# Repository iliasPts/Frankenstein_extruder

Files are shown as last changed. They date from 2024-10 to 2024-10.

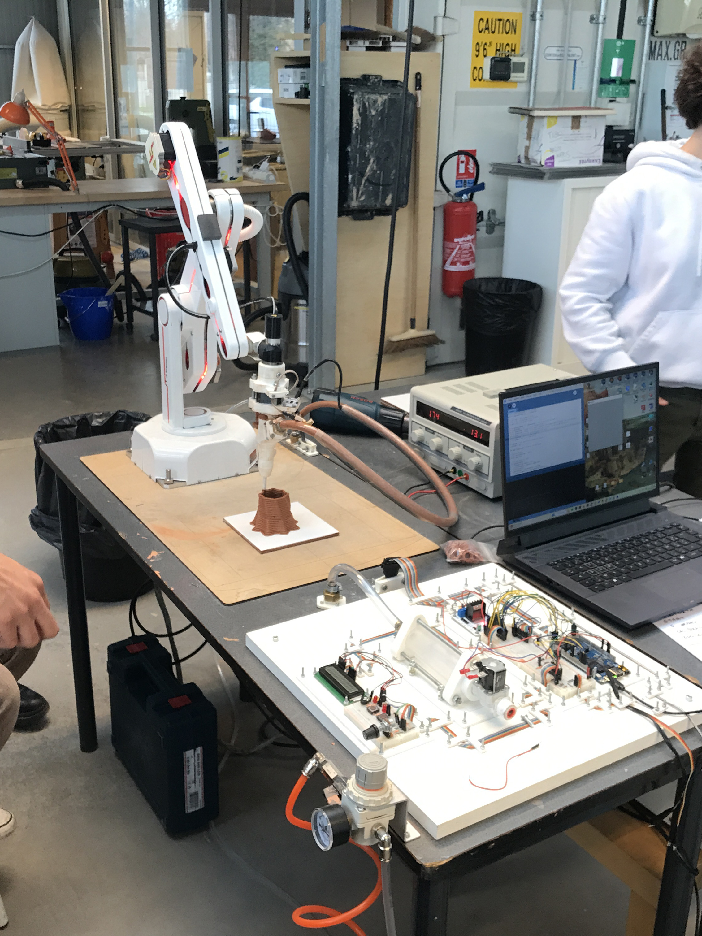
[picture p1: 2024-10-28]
Photos/Photo 2.jpg

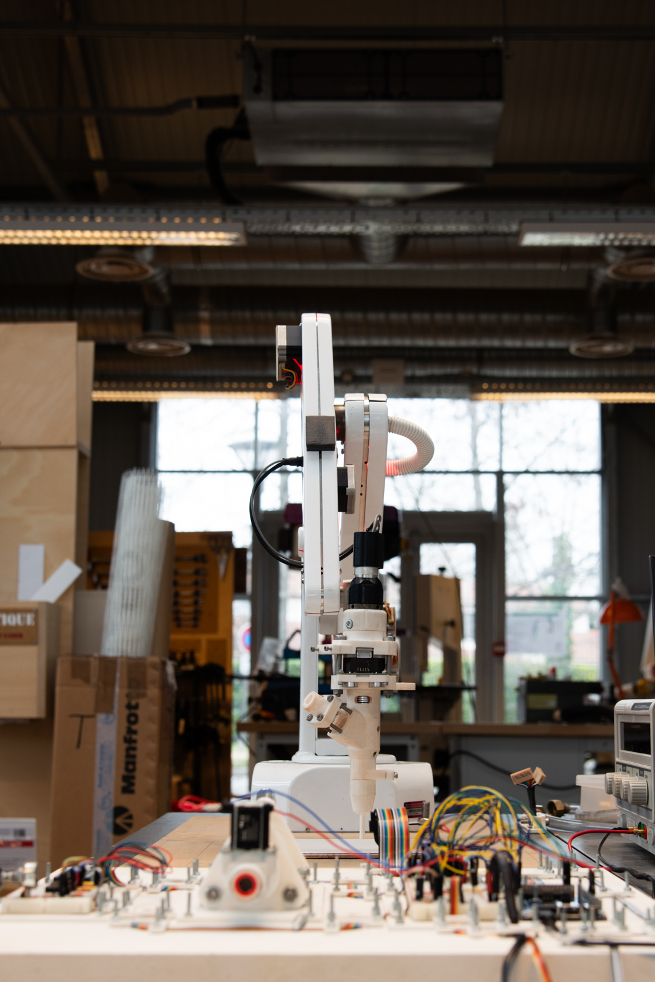
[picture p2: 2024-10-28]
Photos/Photo 5.jpg

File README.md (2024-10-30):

# Frankenstein_extruder
#### Frankenstein is an extruder built for modularity and versatility. Designed with affordability in mind, it’s initially tailored for articulated robots but adaptable to various numerically controled machines, including 3D printers.

Its distinctive feature is the complete accessibility of its components, fully exposed to the view like a body laid open for dissection. This openness allows users to configure countless setups by rearranging electronic, pneumatic, and hose connections.  This modularity is also made possible by the implementation of new programs (in arduino format) enabling new functions. In this way, the system can be expanded by adding new components (e.g. extrusion control sensors) that take advantage of the many electronic lines left available for this very purpose.

Beyond flexibility, Frankenstein is designed for interactive operation (with operators or data exterior to the system), incorporating multiple input and output interfaces (buttons, knobs, LCD displays, sensors, etc.), all programmable to meet specific user needs. This makes it particularly valuable in educational and research contexts.

#### Frankenstein is therefore not an extruder driven by precision or reliability, but by exploration, creativity and serendipity. In the words of philosopher Gilbert Simondon, it's a machine, unfinished, open and imperfect.

IMG_4761B

## License 
### [Attribution-ShareAlike 4.0 International](https://creativecommons.org/licenses/by-sa/4.0/)
<a rel="license" href="http://creativecommons.org/licenses/by-sa/4.0/">
  
</a><br />

You are free to:

- Share — copy and redistribute the material in any medium or format for any purpose, even commercially.
- Adapt — remix, transform, and build upon the material for any purpose, even commercially.
- The licensor cannot revoke these freedoms as long as you follow the license terms.

Under the following terms:
- Attribution — You must give appropriate credit , provide a link to the license, and indicate if changes were made . You may do so in any reasonable manner, but not in any way that suggests the licensor endorses you or your use.
- ShareAlike — If you remix, transform, or build upon the material, you must distribute your contributions under the same license as the original.
- No additional restrictions — You may not apply legal terms or technological measures that legally restrict others from doing anything the license permits.

## Contact
#### Ilias Poutsiakas
insta: https://www.instagram.com/ilias_poutsiakas/
mail: ilias.poutsiakas@gmail.com

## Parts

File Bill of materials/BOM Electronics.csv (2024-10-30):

Item | Qty | Link
Nema 17 stepper motor (a quite powerful one) | 1 | https://www.amazon.fr/s?k=nema+17+stepper+motor
Ultrasonic distance sensor | 1 | https://www.amazon.fr/s?k=ultrasonic+distance+sensor
ATMEGA 2560 board (Arduino or equivalent) | 1 | https://www.amazon.fr/s?k=atmega+2560
L298N Dual H Bridge DC Stepper Motor Driver | 1 | https://www.amazon.fr/s
12V DC Solenoid Water Valve | 1 | https://www.amazon.fr/s?k=12V+DC+Solenoid+Water+Valve
16x2 LCD screen | 1 | https://www.amazon.fr/s?k=16X2+lcd+screen
400 point solderless breadboard | 1 | https://www.amazon.fr/s?k=400+point+bradboard
830 point solderless breadboard | 1 | https://www.amazon.fr/s?k=830+point+bradboard
TIP120 darlington transistor | 1 | https://www.amazon.fr/s?k=TIP120+Darlington+Transistor
1N4001 diode (1A 50V) | 1 | https://www.amazon.fr/s?k=1N4001+Diode+%E2%80%93+1A+50V
1K Ohm Resistor | 1 | https://www.amazon.fr/s?k=1K+Ohm+Resistor
220 Ohm Resistor | 6 | https://www.amazon.fr/s?k=220+%E2%84%A6+Resistor
B50K 50K Ohm Potentiometer | 1 | https://www.amazon.fr/s?k=B50K+50K+Ohm+Potentiometer
10k Ohm rheostat potentiometer for breadboard | 1 | https://www.amazon.fr/s?k=10k+Ohm+rheostat+potentiometer+for+breabdoard
3V light emitting diode | 3 | https://www.amazon.fr/s?k=3V+light+emitting+diode
Breadboard micro button switch | 3 | https://www.amazon.fr/s?k=Breadboard+micro+button+switch
Momentary push button | 2 | https://www.amazon.fr/s?k=momentary+push+button
12V 2A power supply (ideally a variable one) | 1 | https://www.amazon.fr/s?k=12v+2a+power+supply
Jumper wire kit (various length and type, refer to the photos) | 1 | https://www.amazon.fr/s?k=jumper+cable+kit
Flat ribbon cable 16 pin minimum (2m) | 1 | https://www.amazon.fr/s?k=flat+ribbon+cable
16 pin IDC connector | 1 | https://www.amazon.fr/s?k=16+PIN+idc+conector
Male Female Spade Wire Connectors Crimp Terminal | 2 | https://www.amazon.fr/s
16 pin cable 4m | 1 | https://www.amazon.fr/s?k=16+pin+cable
2 pin cable 2m | 1 | https://www.amazon.fr/s?k=2+pin+cable
IC cable male/female 4 pins | 5 | https://www.amazon.fr/s?k=IC+cable+male%2Ffemale+4pins
IC cable male/female 5 pins | 2 | https://www.amazon.fr/s?k=IC+cable+male%2Ffemale+5pins
IC cable male/female 2 pins | 2 | https://www.amazon.fr/s?k=IC+cable+male%2Ffemale+2pins
Heat shrink set | 1 | https://www.amazon.fr/s?k=Heat+shrink+set

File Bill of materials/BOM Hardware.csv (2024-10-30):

Item | Qty | Link
M3 hexagonal screw & bolt kit (varius lengths) | 2 | https://www.amazon.fr/s?k=m3+bolts+and+nuts+six+sided+hollow
M5 hexagonal screw & bolt kit (varius lengths) | 2 | https://www.amazon.fr/s?k=m5+bolts+and+nuts+six+sided+hollow
M5 threaded rod (2m) | 1 | https://www.amazon.fr/s?k=threaded+rod+m4
M4 nuts | 1 | https://www.amazon.fr/s?k=m4+nuts&crid=3RAWGUUNQ4C7E&sprefix=m4+nuts%2Caps%2C106&ref=nb_sb_noss_1
M6 threaded rod (2m) | 3 | https://www.amazon.fr/s?k=m6+threaded+rod
Stepper motor flexible coupler | 1 | https://www.amazon.fr/s?k=stepper+motor+flexible+coupler
Endless screw 6x90mm (head must be sawed off) | 1 | https://www.amazon.fr/s?k=screw+6x90&crid=5Z80MVD5M6ZE&sprefix=screw+6x90%2Caps%2C71&ref=nb_sb_noss
20ml ceringue | 1 | https://www.amazon.fr/s?k=20ml+ceringue
150ml ceringue ( internal piston must be sawed off) | 2 | https://www.amazon.fr/s?k=150ml+ceringue
Flexible silicone hose (5m) | 1 | https://www.amazon.fr/s?k=fliexible+silicone+hose+14mm
Hose Connector Ø12 - Female Rotating 15 x 21 | 8 | https://www.amazon.fr/s?i=diy
Hose clamps | 8 | https://www.amazon.fr/s?k=hose+clamp+8MM&i=diy
1/4" bsp female thread pneumatic connector | 1 | https://www.amazon.fr/s?k=1%2F4%22+bsp+female+thread+pneumatic+connector
15X21 rubber seals | 10 | https://www.amazon.fr/s?k=rubber+seals+15X21
Brass reduction 12/17 male to 15/21 female | 1 | https://www.amazon.fr/s?k=Brass+reduction+12%2F17+male+to+15%2F21+female
PVC round rigid tube 40mm (1m) | 1 | https://www.amazon.fr/s?k=pvc+rigid+tube+40mm
MDF panel 440x440x25mm | 1 | https://www.amazon.fr/s?k=25mm+mdf+panel
MDF panel 3mm | 1 | https://www.amazon.fr/s?k=3mm+mdf+panel
PLA 3D printing filament | 1 | https://www.amazon.fr/s?k=PLA&crid=E0GU2528BUEB&sprefix=pla%2Caps%2C95&ref=nb_sb_noss_1
TPU95A flexible printing filament | 1 | https://www.amazon.fr/s?k=TPU95&crid=2TX28584U88YY&sprefix=tpu95%2Caps%2C112&ref=nb_sb_noss_2
Pressure reducer | 1 | https://www.amazon.fr/s?k=pressure+reducer
Air compressor (10bar 50lt recommended | 1 | https://www.amazon.fr/s?k=air+compressor+10+BAR+50lt
Various pneumatic hoses | 1 | https://www.amazon.fr/s?k=pneumatic+hose

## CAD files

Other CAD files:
Electronic controller plans and diagrams/Plans for fabrication/Electronic controller plan.3dm

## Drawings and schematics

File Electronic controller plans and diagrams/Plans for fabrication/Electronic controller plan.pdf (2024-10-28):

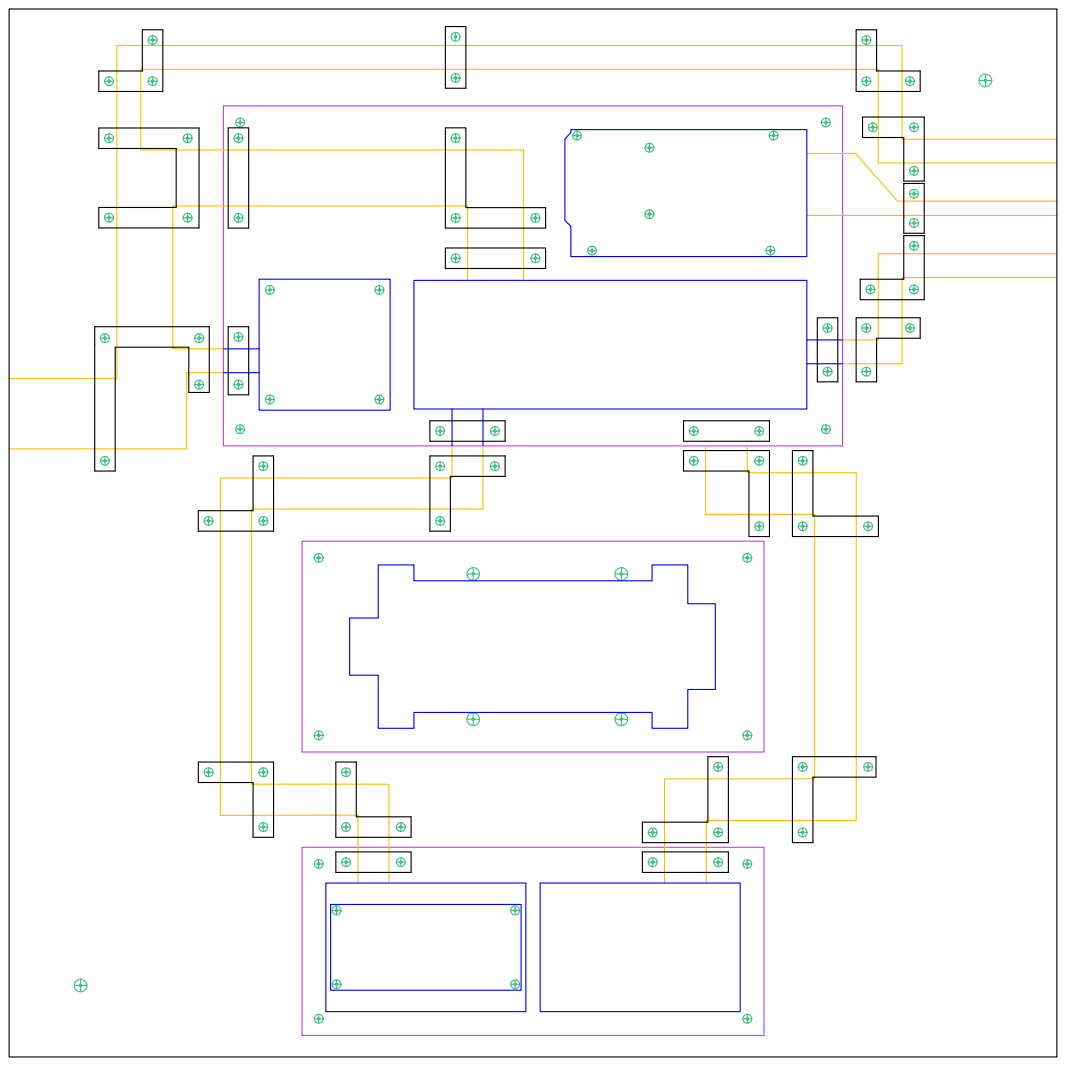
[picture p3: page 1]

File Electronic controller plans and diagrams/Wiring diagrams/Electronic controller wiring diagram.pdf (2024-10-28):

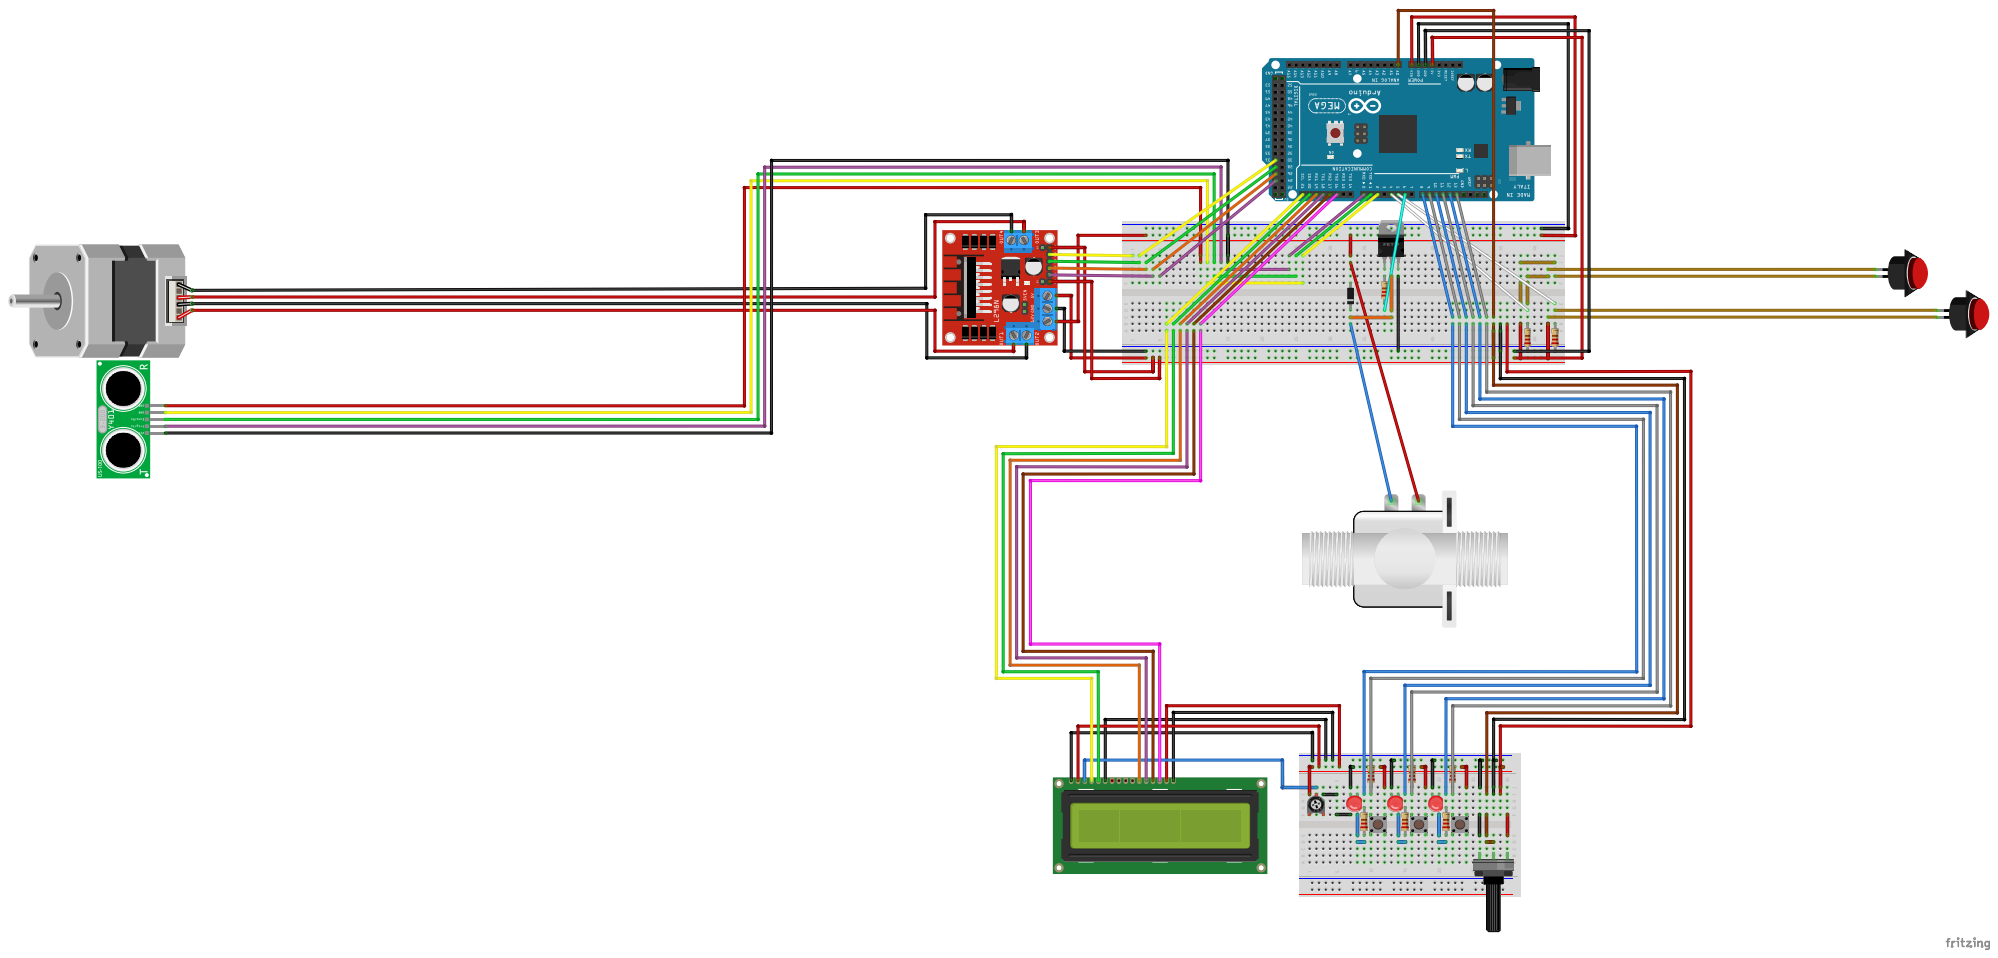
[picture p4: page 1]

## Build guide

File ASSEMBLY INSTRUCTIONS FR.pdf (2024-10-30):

### 5.3.2 L’extrudeur à débit contrôlé

1) Remplir le tank et l’assembler. Pour s’assurer que la matière est bien tassée, qu’elle va bien jusqu’au fond et éviter la formation de bulles il faut mettre le piston, puis remplir le réservoir avec la matière en le tapotant (faire des petits rebondissements sans arrêt sur une surface rigide, par exemple un sol en lino) le piston en bas. Cette procédure permet de tasser la matière au fond du tank et fait remonter les bulles. N’oublie pas les joints et n’hésite pas à bien serrer les boulons afin d’éviter les fuites.

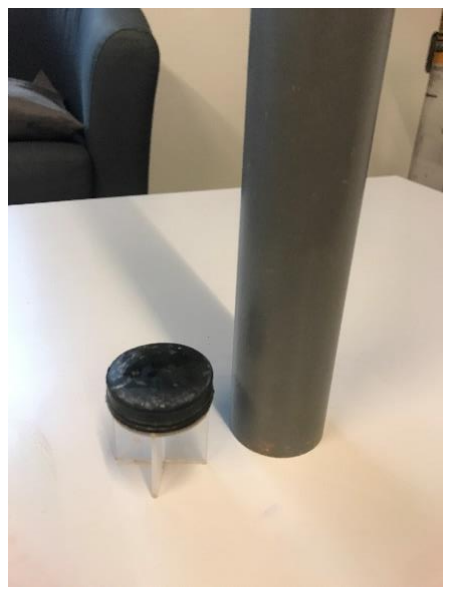
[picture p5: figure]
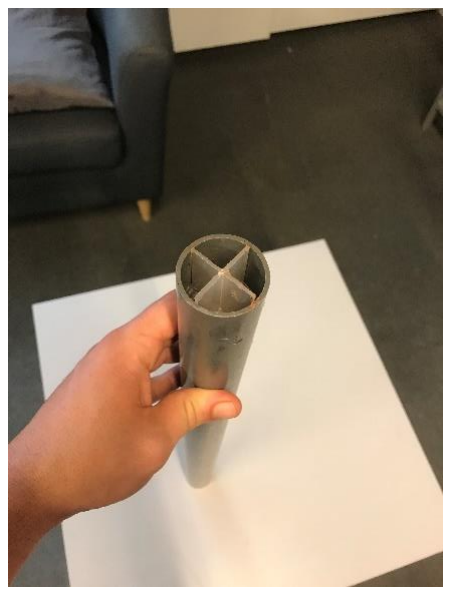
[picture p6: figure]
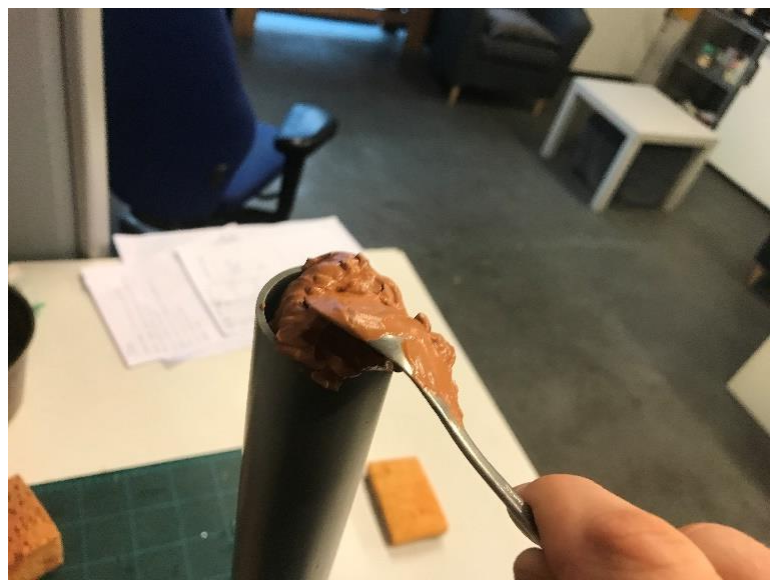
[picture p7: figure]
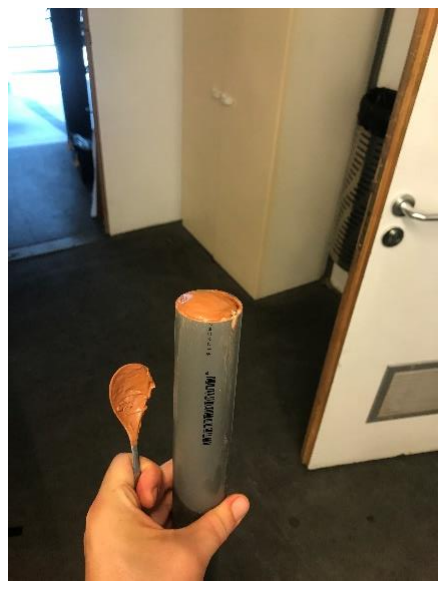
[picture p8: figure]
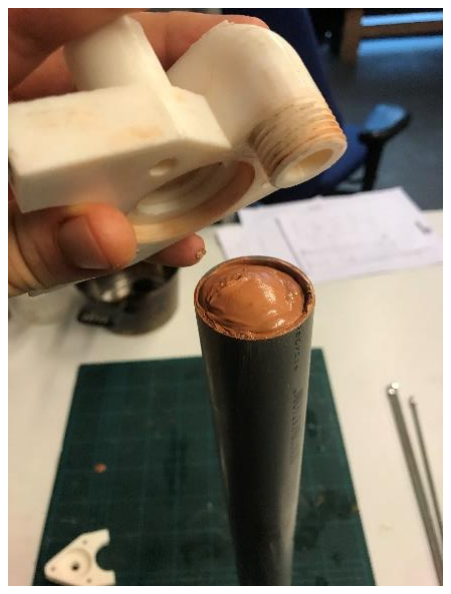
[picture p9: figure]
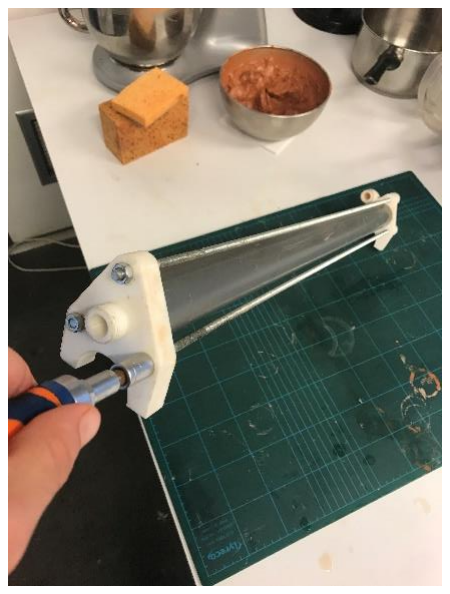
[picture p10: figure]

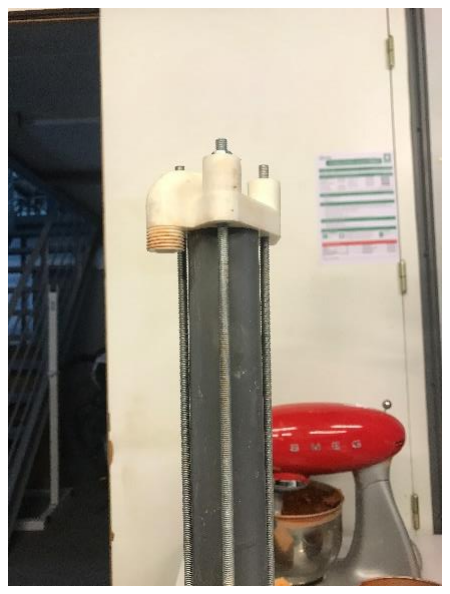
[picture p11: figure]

2) Assembler l’extrudeuse :

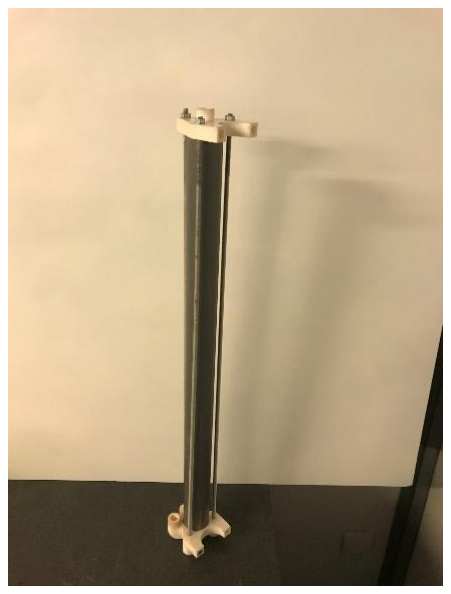
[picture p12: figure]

a) Rassembler les pièces.

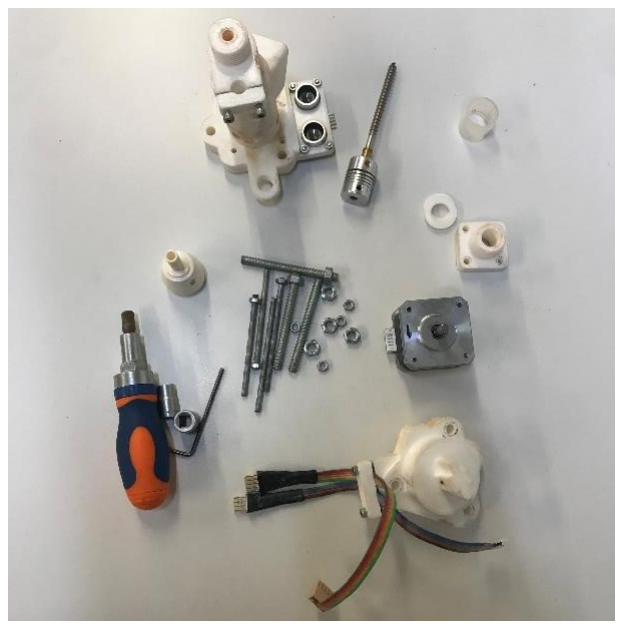
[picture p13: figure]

b) Monter la vis sans fin sur le moteur.

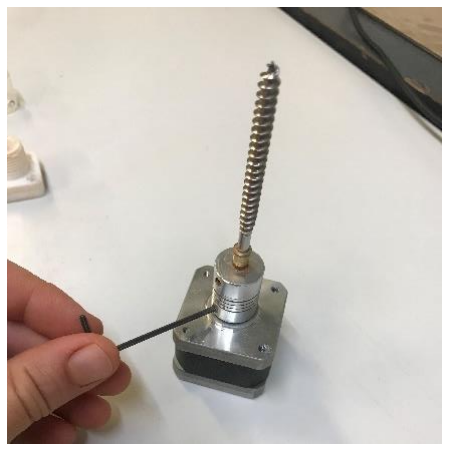
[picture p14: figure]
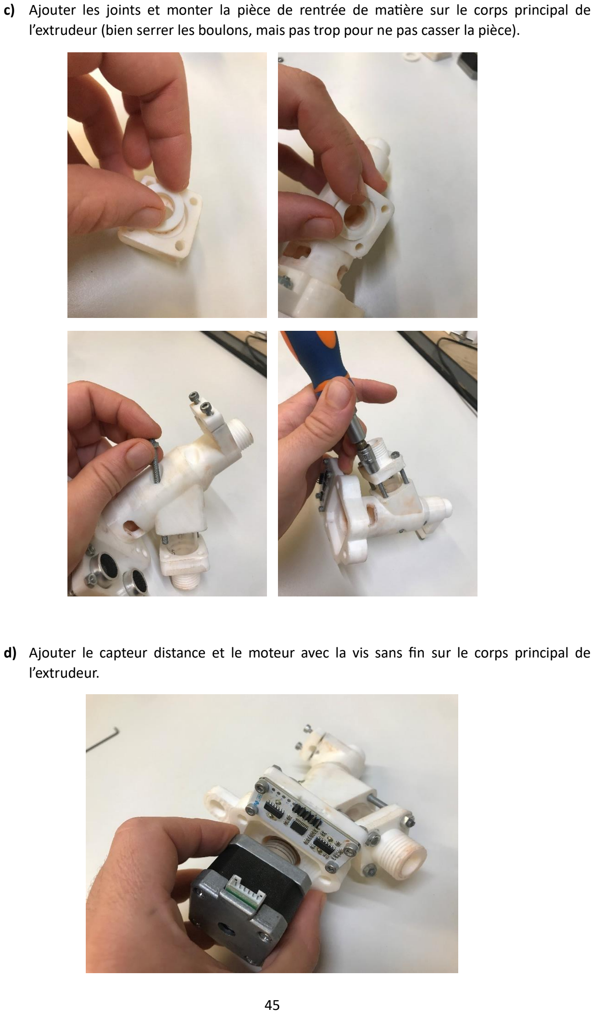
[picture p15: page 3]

c) Ajouter les joints et monter la pièce de rentrée de matière sur le corps principal de l’extrudeur (bien serrer les boulons, mais pas trop pour ne pas casser la pièce).
d) Ajouter le capteur distance et le moteur avec la vis sans fin sur le corps principal de l’extrudeur.

e) Ajouter et visser la partie inférieure, qui prends le moteur en sandwich (bien serrer les boulons car avec les vibrations ils ont tendance à se dévisser, mais pas trop pour ne pas casser la pièce).

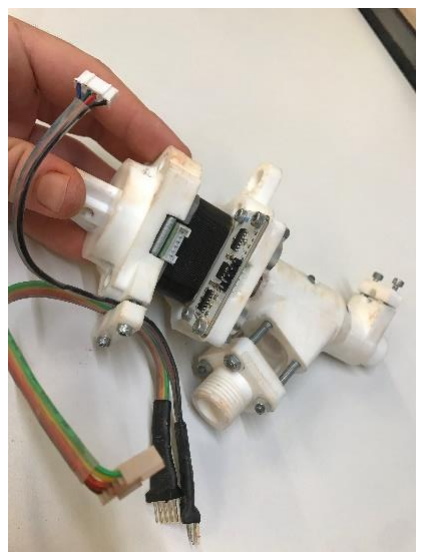
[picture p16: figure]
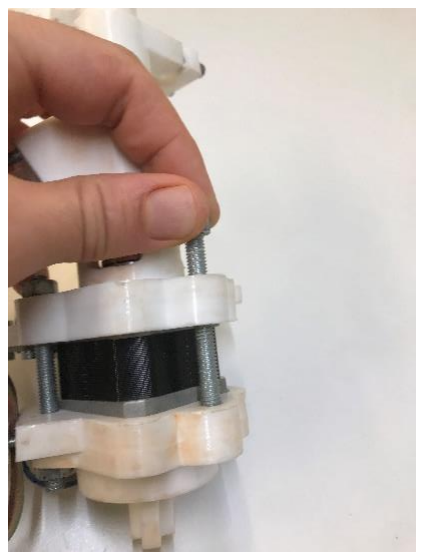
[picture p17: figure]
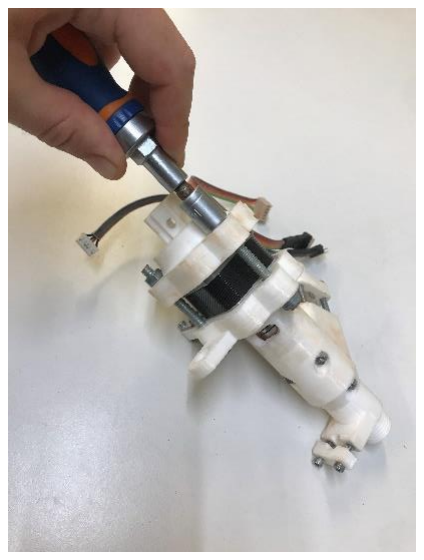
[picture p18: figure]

f) Faire les connections et ajouter une buse (choisis la forme et le diamètre selon tes besoins).

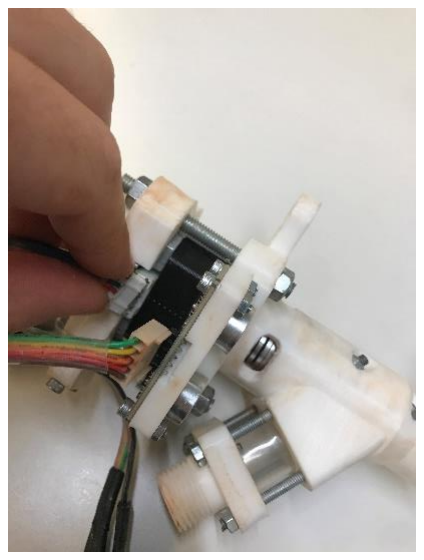
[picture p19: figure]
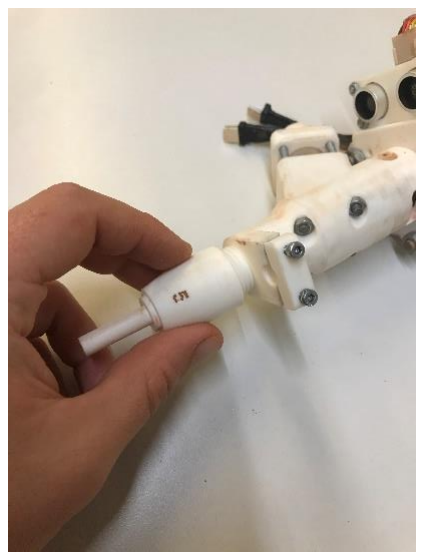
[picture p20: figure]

3) Remplir le compresseur, ajouter une dizaine de bars et le connecter au manomètre qui lui sera réglé autour des 2-4 bars. Ensuite il faudra connecter le manomètre, soit sur la centrale derrière la valve, soit directement sur le tank, cela dépend du montage/programme que tu souhaites utiliser. Tu peux aussi juste dévisser la valve si t’en as pas besoin et quand même passer par la centrale. Dans notre cas nous allons connecter la pression directement sur le tank. Attention : une fois la pression réglée, pense bien à la couper en utilisant la valve rapide sur le manomètre, sinon la matière coulera de partout…

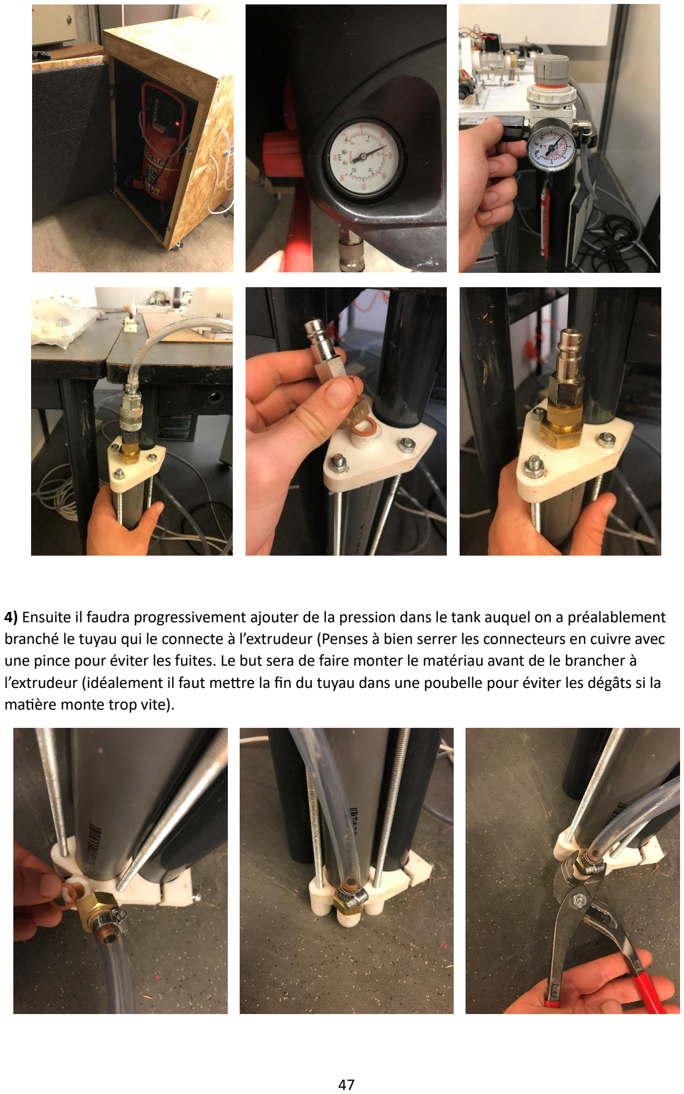
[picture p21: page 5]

4) Ensuite il faudra progressivement ajouter de la pression dans le tank auquel on a préalablement branché le tuyau qui le connecte à l’extrudeur (Penses à bien serrer les connecteurs en cuivre avec une pince pour éviter les fuites. Le but sera de faire monter le matériau avant de le brancher à l’extrudeur (idéalement il faut mettre la fin du tuyau dans une poubelle pour éviter les dégâts si la matière monte trop vite).

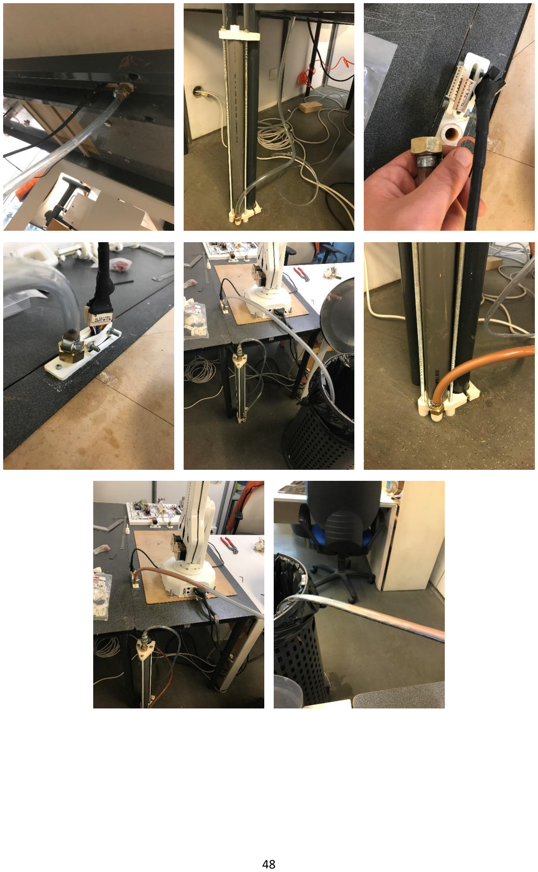
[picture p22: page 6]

5) Monter l’extrudeuse sur le robot en position READY2.

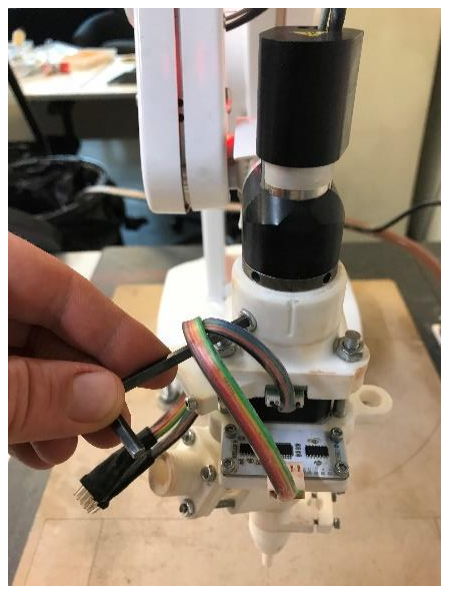
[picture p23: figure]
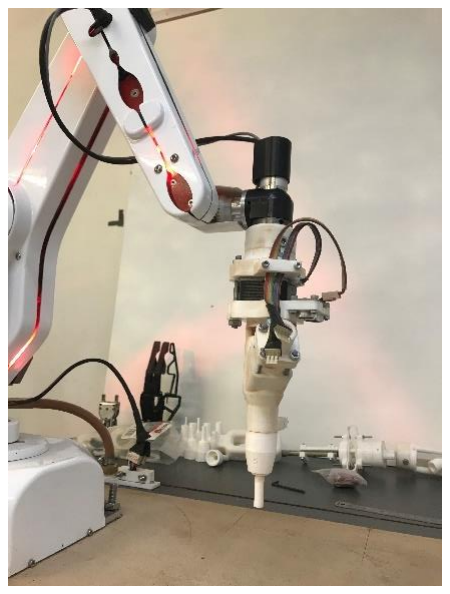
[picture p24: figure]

6) Brancher le tuyau de matière et les différents câbles (attention, si ton programme n’utilise pas de capteur distance, ne le connecte pas, car il risque de bruler).

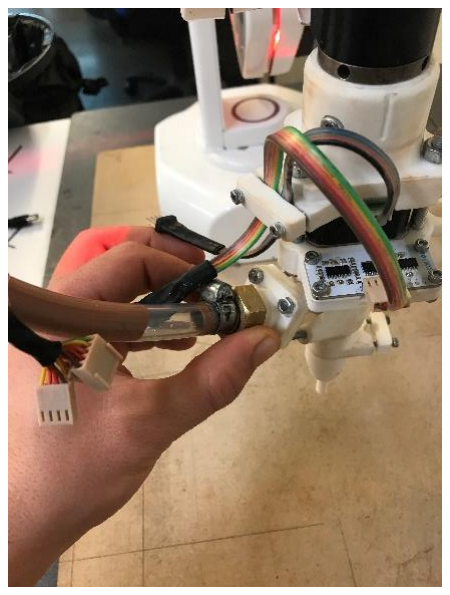
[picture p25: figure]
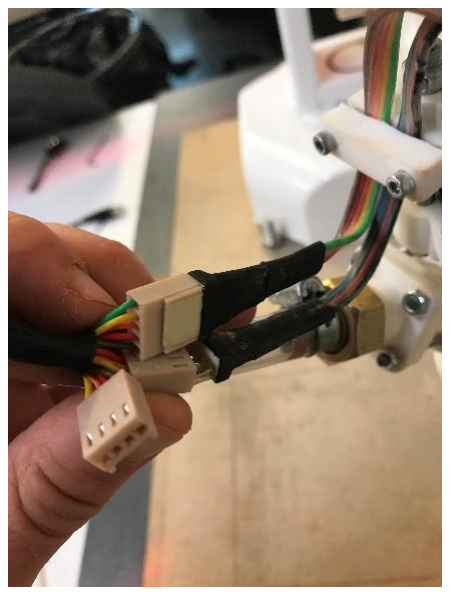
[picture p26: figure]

7) Brancher la centrale en USB sur le PC et l’alimenter en 12v avec le transformateur. Téléverser ensuite le programme dans la centrale.

Tu as le choix entre six programmes tous un peu différents, présents ici …\STARTER PACK CELLULE
ROBOTIQUE MAP-ARIA\4.OUTILLAGE (MODELES POUR FABRICATION ET CODES ARDUINO)\1.CODES ARDUINO POUR CELLULE MODULABLE .

Nous n’allons pas tous les décrire ici. Afin de trouver lequel convient le mieux à ton usage tu peux ouvrir les codes, les premières lignes sont des commentaires prévus pour décrire le fonctionnement et les particularités de chaque code. Tu peux également te référer au titre de chaque fichier pour aller plus vite.

Pour ce tuto nous allons utiliser le programme no. 10 qui permet de lancer l’extrusion en appuyant sur un bouton ainsi que de régler son débit avec un potentiomètre.

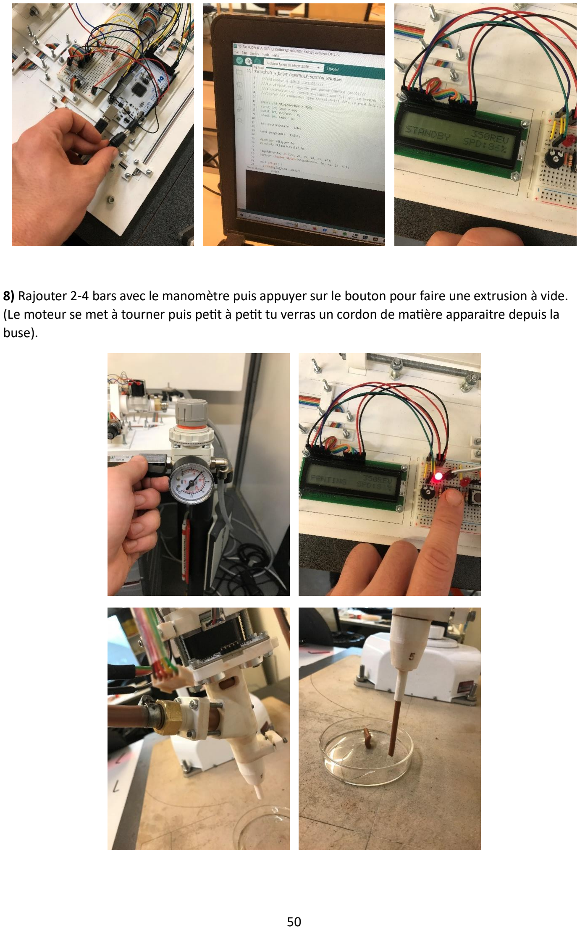
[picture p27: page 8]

8) Rajouter 2-4 bars avec le manomètre puis appuyer sur le bouton pour faire une extrusion à vide. (Le moteur se met à tourner puis petit à petit tu verras un cordon de matière apparaitre depuis la buse).

9) Tu es prêt à lancer ta route. Une fois le robot en mouvement, relance l’extrusion en appuyant sur le bouton de la centrale. Il faudra rester vigilant tout au long de l’impression car il faudra potentiellement faire des modifications sur la vitesse du moteur (potentiomètre de la centrale) ou la pression sur le manomètre afin de bien régler l’extrusion.

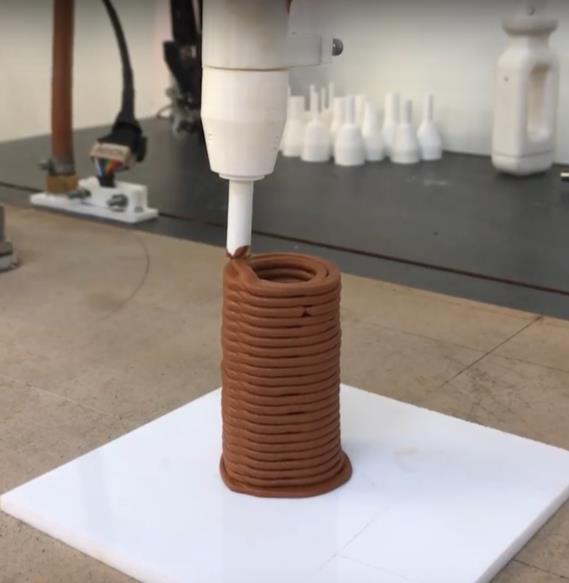
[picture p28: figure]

## 6. Les grandes étapes d’une Impression 3D d’un artefact en argile

avec l’extrudeur à débit contrôlé, de A à Z.

Maintenant que nous avons vu en détail la totalité des composants de la cellule, les logiciels, la programmation du robot, l’utilisation des outils etc., nous allons résumer leur rôle dans le processus en détaillant le cas de l’impression 3D argile avec l’extrudeur à débit contrôlé. Ça te permettra de voir comment les étapes s’enchainent et à quel moment chaque méthode arrive dans le processus et comment elle s’articule avec les autres. Dans cette partie nous allons donc détailler comment se déroule une impression 3D du tout début à la toute fin. Nous n’allons pas détailler les outils et les méthodes car nous l’avons fait plus haut mais juste lister les étapes. Si par exemple tu as des questions lorsque nous allons voir les étapes ou la route est programmée, tu peux te référer à la partie 4 qui détaille cette partie.

1) Prépare ton argile. Pour préparer ton argile il suffit de le mettre dans le malaxeur avec de l’eau et de le faire tourner jusqu’à ce qu’il adopte la bonne viscosité. Il n’y a pas de règle pour la fluidité. Il faut qu’il soit assez fluide pour passer dans les tuyaux mais il doit être assez solide et visqueux pour tenir lors de l’impression. Généralement, un bon test à faire est de prendre une seringue puis l’extruder à la main. Si le cordon sort sans effort et peut atteindre 5-10cm sans se couper c’est qu’il a la bonne consistance.

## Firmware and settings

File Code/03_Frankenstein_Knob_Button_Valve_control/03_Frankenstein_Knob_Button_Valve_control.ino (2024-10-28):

/// Controlled flow extruder ///
/// Speed is regulated by potentiometer (knob) ///
/// The extrusion starts only when both the first and second buttons are pressed ///
/// The first button activates the valve that introduces compressed air into the system. The second starts the motor rotation ///
/// Avoid Serial.Print type commands in the void loop to take full advantage of the motor speed ///
/// Do not connect the distance sensor as it is not intended for this program; otherwise, it may burn out ///

const int StepsPerRev = 400;
const int Knob = A0;
const int ButtonA = 9;
const int ButtonB = 11;
const int LedA = 8;
const int LedB = 10;
const int Valve = 14;

int ButtonAState = LOW;
int ButtonBState = LOW;

bool programAOn = false;
bool programBOn = false;

#include <Stepper.h>
#include <LiquidCrystal.h>

LiquidCrystal lcd(23, 22, 25, 24, 27, 26);
Stepper stepper_NEMA17(StepsPerRev, 50, 51, 52, 53);

void setup() {
  pinMode(ButtonA, INPUT);
  pinMode(ButtonB, INPUT);
  pinMode(LedA, OUTPUT);
  pinMode(LedB, OUTPUT);
  pinMode(Valve, OUTPUT);
  Serial.begin(9600);
  Serial.println("Controlled flow extruder");
  Serial.println("Speed is regulated by potentiometer (knob)");
  Serial.println("The extrusion starts only when both the first and second buttons are pressed");
  Serial.println("The first button activates the valve that introduces compressed air into the system. The second starts the motor rotation");
  Serial.println("Avoid Serial.Print type commands in the void loop to take full advantage of the motor speed");
  Serial.println("Do not connect the distance sensor as it is not intended for this program; otherwise, it may burn out");
  lcd.begin(8, 2);
  lcd.print("E.A.D.C. BUTTON");
  lcd.setCursor(0, 1);
  lcd.print("+VALV +KNOB");
  delay(2000);
  lcd.clear();
  lcd.print("VALVE:OFF ");
  lcd.print(StepsPerRev);
  lcd.print("REV");
  lcd.setCursor(0, 1);
  lcd.print("STANDBY");
  lcd.print("  SPD:");
}

void loop() {
  int sensorReading = analogRead(Knob);
  int motorSpeed = map(sensorReading, 0, 1023, 0, 99);

  lcd.setCursor(14, 1);
  lcd.print(" ");
  lcd.setCursor(13, 1);
  lcd.print(motorSpeed);
  lcd.setCursor(15, 1);
  lcd.print("%");

  int ButtonAReading = digitalRead(ButtonA);
  if (ButtonAReading != ButtonAState) {
    ButtonAState = ButtonAReading;
    if (ButtonAState == HIGH) {
      programAOn = !programAOn;
      if (programAOn) {
        digitalWrite(LedA, HIGH);
        lcd.setCursor(6, 0);
        lcd.print("ON ");
        digitalWrite(Valve, HIGH);
      } else {
        digitalWrite(LedA, LOW);
        lcd.setCursor(6, 0);
        lcd.print("OFF");
        digitalWrite(Valve, LOW);
      }
    }
  }

  int ButtonBReading = digitalRead(ButtonB);
  if (ButtonBReading != ButtonBState) {
    ButtonBState = ButtonBReading;
    if (ButtonBState == HIGH) {
      programBOn = !programBOn;
      if (programBOn) {
        digitalWrite(LedB, HIGH);
        lcd.setCursor(0, 1);
        lcd.print("PRINTING");
      } else {
        digitalWrite(LedB, LOW);
        lcd.setCursor(0, 1);
        lcd.print("STANDBY");
      }
    }
  }

  if (programBOn) {
    if (motorSpeed > 0) {
      stepper_NEMA17.setSpeed(motorSpeed);
      stepper_NEMA17.step(StepsPerRev / 100);
    }
  }
}

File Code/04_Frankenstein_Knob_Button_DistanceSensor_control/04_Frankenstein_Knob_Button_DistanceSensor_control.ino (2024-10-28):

/// Controlled flow extruder ///
/// Speed is regulated by potentiometer (knob) ///
/// The extrusion starts only when the first button is pressed and the sensor is at the correct distance (below the defined value) ///
/// Avoid Serial.Print type commands in the void loop to take full advantage of the motor speed ///

const int StepsPerRev = 400;
const int Knob = A0;
const int ButtonA = 9;
const int LedA = 8;
const int LedB = 10;
const int Echo = 3;
const int Trigger = 2;
const int ExtrusionDistance = 15;

int ButtonAState = LOW;
bool programOn = false;

long duration;
int distance;

#include <Stepper.h>
#include <LiquidCrystal.h>

LiquidCrystal lcd(23, 22, 25, 24, 27, 26);
Stepper stepper_NEMA17(StepsPerRev, 50, 51, 52, 53);

void setup() {
  pinMode(ButtonA, INPUT);
  pinMode(LedA, OUTPUT);
  pinMode(LedB, OUTPUT);
  pinMode(Trigger, OUTPUT); 
  pinMode(Echo, INPUT);
  Serial.begin(9600);
  Serial.println("Controlled flow extruder");
  Serial.println("Speed is regulated by potentiometer (knob)");
  Serial.println("The extrusion starts only when the first button is pressed and the sensor is at the correct distance (below the defined value)");
  Serial.println("Avoid Serial.Print type commands in the void loop to take full advantage of the motor speed");
  lcd.begin(8, 2);
  lcd.print("E.A.D.C. BUTTON");
  lcd.setCursor(0, 1);
  lcd.print("+DIST +KNOB");
  delay(2000);
  lcd.clear();
  lcd.print("DIST:");
  lcd.setCursor(10, 0);
  lcd.print(StepsPerRev);
  lcd.print("REV");
  lcd.setCursor(0, 1);
  lcd.print("STANDBY  SPD:");
}

void loop() {
  int sensorReading = analogRead(Knob);
  int motorSpeed = map(sensorReading, 0, 1023, 0, 99);

  digitalWrite(Trigger, LOW);
  delayMicroseconds(1);
  digitalWrite(Trigger, HIGH);
  delayMicroseconds(10);
  duration = pulseIn(Echo, HIGH);
  distance = duration * 0.034 / 2;

  lcd.setCursor(5, 0);
  lcd.print("   ");
  lcd.setCursor(5, 0);
  lcd.print(distance);
  lcd.setCursor(14, 1);
  lcd.print(" ");
  lcd.setCursor(13, 1);
  lcd.print(motorSpeed);
  lcd.setCursor(15, 1);
  lcd.print("%");

  int ButtonAReading = digitalRead(ButtonA);
  if (ButtonAReading != ButtonAState) {
    ButtonAState = ButtonAReading;
    if (ButtonAState == HIGH) {
      programOn = !programOn;
      if (programOn) {
        lcd.setCursor(0, 1);
        lcd.print("READY2PR");
        digitalWrite(LedA, HIGH);
      } else {
        lcd.setCursor(0, 1);
        lcd.print("STANDBY ");
        digitalWrite(LedA, LOW);
      }
    }
  }

  if (programOn) {
    if (distance < ExtrusionDistance && distance > 0) {
      digitalWrite(LedB, HIGH);
      stepper_NEMA17.setSpeed(motorSpeed);
      stepper_NEMA17.step(StepsPerRev / 100);
      digitalWrite(LedB, LOW);
    }
  }
}

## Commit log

2024-10-28 Create CAD FILES
2024-10-28 Update CAD FILES
2024-10-28 Rename CAD FILES to CAD & 3D PRINTING FILES
2024-10-28 Rename CIRCUIT ELECTRONIQUE FINAL.fzz to Electronic diagram.fzz
    [Electronic diagram.fzz]
2024-10-29 Update BOM Hardware.csv
    [BOM Hardware.csv]
2024-10-30 Update CAD & 3D PRINTING FILES
2024-10-30 Update BOM Electronics.csv
    [BOM Electronics.csv]
2024-10-30 Update and rename BOM Electronics.csv to BOM Electronics.csv
    [BOM Electronics.csv]
2024-10-30 Rename Mounting instructions FR.pdf to ASSEMBLY INSTRUCTIONS FR.pdf

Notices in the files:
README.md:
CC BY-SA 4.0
